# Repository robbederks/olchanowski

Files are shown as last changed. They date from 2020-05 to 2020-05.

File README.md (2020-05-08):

# Olchanowski
## Fixing the Zortrax M200 electronics
The Zortrax M200's mechanical design is great. It's electronics and software is not.
Let's fix that!

### Checklist
- [X] Processor
- [X] 4 stepper drivers
- [X] Ethernet
- [X] Fan control
- [X] 3 end stops
- [X] "senser"
- [X] RGB LED strip control
- [X] Heated bed
  - [X] Driver
  - [X] Thermocouple
- [X] Power input
- [X] Power regulation
- [X] USB
- [X] UI cable
  - [X] Connector
  - [X] OLED panel (UG-5664ALBEF01)
  - [X] Beeper
  - [X] Rotary encoder
  - [X] SD card
- [X] Extruder cable
  - [X] Connector (1-281742-2)
  - [X] Stepper
  - [X] Heater
  - [X] Thermocouple
  - [X] Fans
- [X] ICSP: UART
- [X] Filament sensor
- [X] LEDs
  - [X] GPIOs
  - [X] Voltage rail
  - [X] Heaters

## Version 1: Order list
| Description | MPN | QTY |
|---|---|-----|
| Extruder cable connector | 1-281742-2 | 1 |
| Heated bed connector | 1744428-4 | 1 |
| LCD connector | 302-S201 | 1 |
| Ethernet jack | ARJM11D7-009-AB-ER2-T | 1 |
| End switch + FAN + HB thermistor connector | B2B-XH-AM(LF)(SN) | 5 |
| Diode | BAT60AE6327HTSA1 | 2 |
| 470pF 0402 | C0402C471K5RACTU | 2 |
| 22nF 0402 | GRM155R71H223KA12J | 4 |
| 100 Ohm 0402 | CRG0402F100R | 2 |
| 10 kOhm 0402 | CRG0402F10K | 26  |
| 1 kOhm 0402 | CRG0402F1K | 3 |
| 1.5 kOhm 0402 | CRG0402F1K5 | 2 |
| 1 Mohm 0402 | CRG0402F1M | 1 |
| 22 Ohm 0402 | CRG0402F22R | 4 |
| 2.4 kOhm 0402 | CRG0402F2K4 | 1 |
| 33 Ohm 0402 | CRG0402F33R | 2 |
| 4.7 kOhm 0402 | CRG0402F4K7 | 2 |
| 50 Ohm 0402 | CRG0402F50R | 4 |
| 12MHz crystal | CX3225SB12000H0PSTC1  | 1 |
| 25MHz crystal | CX3225SB25000H0FLJCC  | 1 |
| 12.1 kOhm | ERJ-2RKF1212X | 1 |
| Push buttons | EVQ-Q2Y03W | 2 |
| 12pF 0402 | GRM1555C1E120GA01D | 10  |
| 4.7uF 0402 | GRM155R61A475MEAAD | 13  |
| 100nF 0402 | GRM155R61H104KE19D | 45  |
| 10uF 0805 | GRM21BR6YA106ME43L | 8 |
| Current sense resistor 0.1 Ohm 1206 | KRL1632E-M-R100-F-T5  | 8 |
| LM5551 | LM5111-1MX/NOPB | 1 |
| LPC1768 | "LPC1769FBD100,551" | 1 |
| LEDs 0603 | LTST-C190TBKT | 7 |
| Inductor | MLZ1608A1R0WT000 | 1 |
| PCA9306DCTR | PCA9306DCTR | 1 |
| 6 pin header | PPTC061LFBN-RC | 1 |
| Power MOSFET | SIJA58DP | 2 |
| N-Ch MOSFET | "SSM3K329R,LF" | 6 |
| Stepper driver | TMC2209-LA | 4 |
| 220uF elcaps | UCW1V221MNL1GS | 8 |
| Stepper + RGB + filament sensor connectors | B4B-XH-A(LF)(SN) | 5 |
| USB-C female connector | DX07S024XJ1R1100 | 1 |
| Power connector | 282814-4 | 1 |
| Power module | TPSM53602 | 1 |
| P-Ch MOSFET | DMP3099L-13 | 1 |
| Ethernet PHY | LAN8720A-CP-TR-ABC | 1 |
| Inverter | 74HC1G04 | 1 |
| 3.3V regulator | NCP5661MN33T2G | 1 |
| Senser connector | B3B-XH-A(LF)(SN) | 1 |

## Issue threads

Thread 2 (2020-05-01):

X1, X2, X3, X4 Part is missing mounting hole

vanillagorillaa, 2020-05-01:
B2B-XH-AMK(LF)(SN) is missing a mounting hole in the board

vanillagorillaa, 2020-05-09:
Fixed in 6538cdf7a0786e43772336199ad8634c6ffd7720

Closed 2020-05-09.

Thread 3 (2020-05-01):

Ethernet connector LED pins in wrong spot

vanillagorillaa, 2020-05-01:
ARJM11D7-009-AB-ER2-T Footprint is wrong. Current footprint uses 10/100/1000 connector footprint

vanillagorillaa, 2020-05-09:
Fixed in 37fe7109c28374d02037d3b275595f5fae3c16f2

Closed 2020-05-09.

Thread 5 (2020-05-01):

Ethernet connector footprint numbering wrong

robbederks, 2020-05-01:

vanillagorillaa, 2020-05-09:
Fixed in 37fe7109c28374d02037d3b275595f5fae3c16f2

Closed 2020-05-09.

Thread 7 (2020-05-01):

AGND not connected on P1

robbederks, 2020-05-01:
Also connect NC pins to GND like in datasheet (https://www.ti.com/lit/ds/symlink/tpsm53602.pdf?ts=1588302774740)

vanillagorillaa, 2020-05-08:
Fixed in 749eeb49f01eb6fa2927ce801f29494a110230ea

Closed 2020-05-08.

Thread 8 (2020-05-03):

Pin P0_27 and P0_28 are open-drain only: no LED driving!

robbederks, 2020-05-03:

vanillagorillaa, 2020-05-09:
Fixed in f67002b0d46e6c94cf34e9f857e3886063b88d9a

Closed 2020-05-09.

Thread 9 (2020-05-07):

Stepper connector winding pinout is wrong

robbederks, 2020-05-07:

vanillagorillaa, 2020-05-08:
Fixed in 95ee329ae1723655891ae612e65790c3f3b5e32d

Closed 2020-05-08.

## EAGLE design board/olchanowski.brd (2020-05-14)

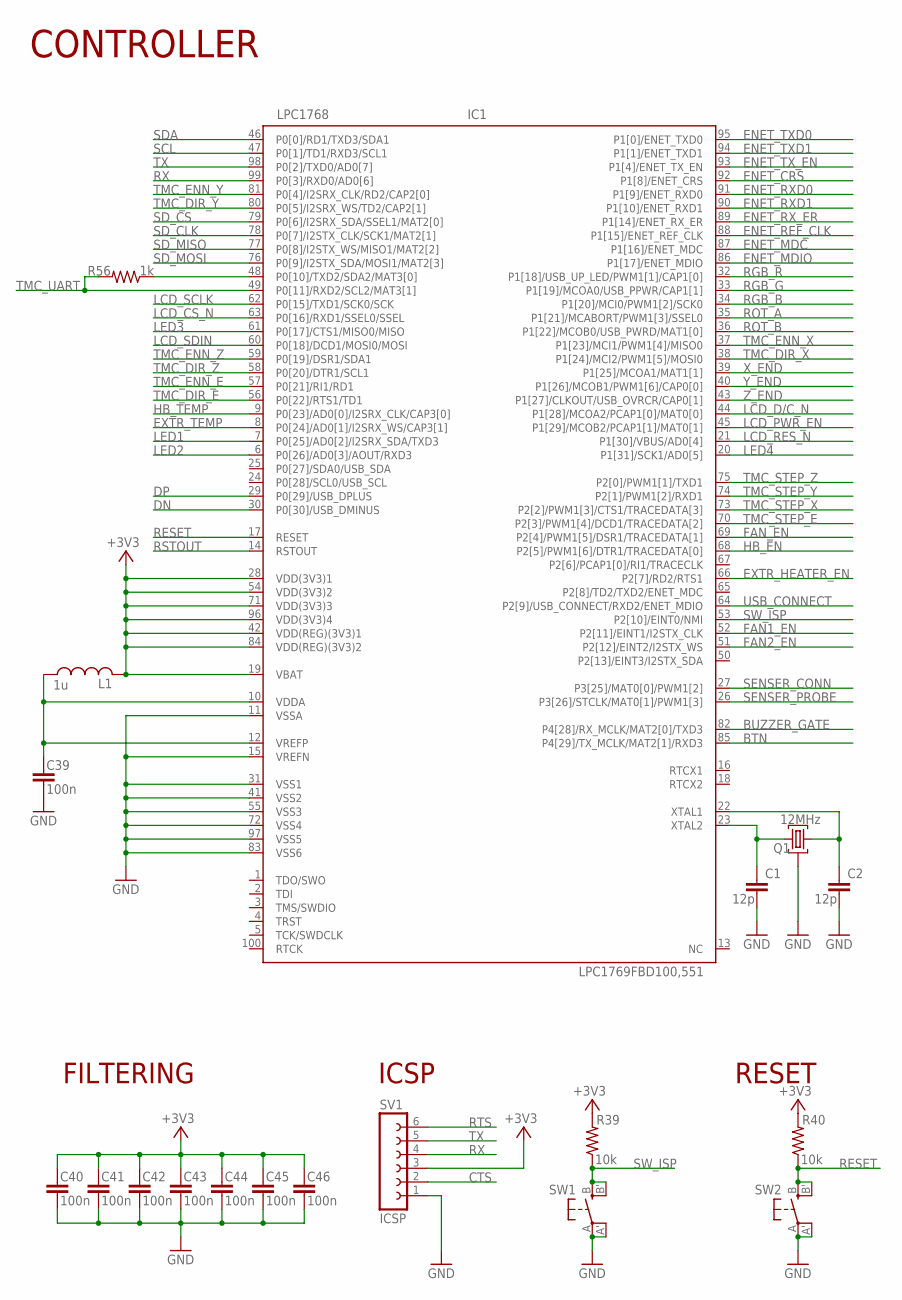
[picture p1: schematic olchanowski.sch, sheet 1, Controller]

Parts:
C1, C2: C; 0402; MPN GRM1555C1E120GA01D
C39, C40, C41, C42, C43, C44, C45, C46: C; 0402; MPN GRM155R61H104KE19D
IC1: LPC1768; LQFP100-14X14; MPN LPC1769FBD100,551
L1: L-USL0603; L0603; MPN MLZ1608A1R0WT000
Q1: 12MHz; CX3225SB; MPN CX3225SB12000H0PSTC1
R39, R40: R-US_R0402; R0402; MPN CRG0402F10K
R56: R-US_R0402; R0402; MPN CRG0402F1K
SV1: ICSP; FE06; MPN PPTC061LFBN-RC
SW1, SW2: SPST-2-4PIN; EVQ-Q2; MPN EVQ-Q2Y03W

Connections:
+3V3: C40.2, C41.2, C42.2, C43.2, C44.2, C45.2, C46.2, IC1.19 (VBAT), IC1.28 (VDD(3V3)1), IC1.42 (VDD(REG)(3V3)1), IC1.54 (VDD(3V3)2), IC1.71 (VDD(3V3)3), IC1.84 (VDD(REG)(3V3)2), IC1.96 (VDD(3V3)4), L1.2, R39.2, R40.2, SV1.3; also elsewhere on the board
BTN: IC1.85 (P4[29]/TX_MCLK/MAT2[1]/RXD3); also elsewhere on the board
BUZZER_GATE: IC1.82 (P4[28]/RX_MCLK/MAT2[0]/TXD3); also elsewhere on the board
CTS: SV1.2
DN: IC1.30 (P0[30]/USB_DMINUS); also elsewhere on the board
DP: IC1.29 (P0[29]/USB_DPLUS); also elsewhere on the board
ENET_CRS: IC1.92 (P1[8]/ENET_CRS); also elsewhere on the board
ENET_MDC: IC1.87 (P1[16]/ENET_MDC); also elsewhere on the board
ENET_MDIO: IC1.86 (P1[17]/ENET_MDIO); also elsewhere on the board
ENET_REF_CLK: IC1.88 (P1[15]/ENET_REF_CLK); also elsewhere on the board
ENET_RXD0: IC1.91 (P1[9]/ENET_RXD0); also elsewhere on the board
ENET_RXD1: IC1.90 (P1[10]/ENET_RXD1); also elsewhere on the board
ENET_RX_ER: IC1.89 (P1[14]/ENET_RX_ER); also elsewhere on the board
ENET_TXD0: IC1.95 (P1[0]/ENET_TXD0); also elsewhere on the board
ENET_TXD1: IC1.94 (P1[1]/ENET_TXD1); also elsewhere on the board
ENET_TX_EN: IC1.93 (P1[4]/ENET_TX_EN); also elsewhere on the board
EXTR_HEATER_EN: IC1.66 (P2[7]/RD2/RTS1); also elsewhere on the board
EXTR_TEMP: IC1.8 (P0[24]/AD0[1]/I2SRX_WS/CAP3[1]); also elsewhere on the board
FAN1_EN: IC1.52 (P2[11]/EINT1/I2STX_CLK); also elsewhere on the board
FAN2_EN: IC1.51 (P2[12]/EINT2/I2STX_WS); also elsewhere on the board
FAN_EN: IC1.69 (P2[4]/PWM1[5]/DSR1/TRACEDATA[1]); also elsewhere on the board
GND: C1.2, C2.2, C39.1, C40.1, C41.1, C42.1, C43.1, C44.1, C45.1, C46.1, IC1.11 (VSSA), IC1.15 (VREFN), IC1.31 (VSS1), IC1.41 (VSS2), IC1.55 (VSS3), IC1.72 (VSS4), IC1.83 (VSS6), IC1.97 (VSS5), Q1.GND1 (2), Q1.GND2 (2), SV1.1, SW1.A, SW1.A' (P1), SW2.A, SW2.A' (P1); also elsewhere on the board
HB_EN: IC1.68 (P2[5]/PWM1[6]/DTR1/TRACEDATA[0]); also elsewhere on the board
HB_TEMP: IC1.9 (P0[23]/AD0[0]/I2SRX_CLK/CAP3[0]); also elsewhere on the board
LCD_CS_N: IC1.63 (P0[16]/RXD1/SSEL0/SSEL); also elsewhere on the board
LCD_D/C_N: IC1.44 (P1[28]/MCOA2/PCAP1[0]/MAT0[0]); also elsewhere on the board
LCD_PWR_EN: IC1.45 (P1[29]/MCOB2/PCAP1[1]/MAT0[1]); also elsewhere on the board
LCD_RES_N: IC1.21 (P1[30]/VBUS/AD0[4]); also elsewhere on the board
LCD_SCLK: IC1.62 (P0[15]/TXD1/SCK0/SCK); also elsewhere on the board
LCD_SDIN: IC1.60 (P0[18]/DCD1/MOSI0/MOSI); also elsewhere on the board
LED1: IC1.7 (P0[25]/AD0[2]/I2SRX_SDA/TXD3); also elsewhere on the board
LED2: IC1.6 (P0[26]/AD0[3]/AOUT/RXD3); also elsewhere on the board
LED3: IC1.61 (P0[17]/CTS1/MISO0/MISO); also elsewhere on the board
LED4: IC1.20 (P1[31]/SCK1/AD0[5]); also elsewhere on the board
unnamed: C1.1, IC1.23 (XTAL2), Q1.XTAL1 (1)
unnamed: C2.1, IC1.22 (XTAL1), Q1.XTAL2 (3)
unnamed: C39.2, IC1.10 (VDDA), IC1.12 (VREFP), L1.1
unnamed: IC1.48 (P0[10]/TXD2/SDA2/MAT3[0]), R56.1
RESET: IC1.17 (RESET), R40.1, SW2.B (S), SW2.B' (S1)
RGB_B: IC1.34 (P1[20]/MCI0/PWM1[2]/SCK0); also elsewhere on the board
RGB_G: IC1.33 (P1[19]/MCOA0/USB_PPWR/CAP1[1]); also elsewhere on the board
RGB_R: IC1.32 (P1[18]/USB_UP_LED/PWM1[1]/CAP1[0]); also elsewhere on the board
ROT_A: IC1.35 (P1[21]/MCABORT/PWM1[3]/SSEL0); also elsewhere on the board
ROT_B: IC1.36 (P1[22]/MCOB0/USB_PWRD/MAT1[0]); also elsewhere on the board
RSTOUT: IC1.14 (RSTOUT); also elsewhere on the board
RTS: SV1.6
RX: IC1.99 (P0[3]/RXD0/AD0[6]), SV1.4
SCL: IC1.47 (P0[1]/TD1/RXD3/SCL1); also elsewhere on the board
SDA: IC1.46 (P0[0]/RD1/TXD3/SDA1); also elsewhere on the board
SD_CLK: IC1.78 (P0[7]/I2STX_CLK/SCK1/MAT2[1]); also elsewhere on the board
SD_CS: IC1.79 (P0[6]/I2SRX_SDA/SSEL1/MAT2[0]); also elsewhere on the board
SD_MISO: IC1.77 (P0[8]/I2STX_WS/MISO1/MAT2[2]); also elsewhere on the board
SD_MOSI: IC1.76 (P0[9]/I2STX_SDA/MOSI1/MAT2[3]); also elsewhere on the board
SENSER_CONN: IC1.27 (P3[25]/MAT0[0]/PWM1[2]); also elsewhere on the board
SENSER_PROBE: IC1.26 (P3[26]/STCLK/MAT0[1]/PWM1[3]); also elsewhere on the board
SW_ISP: IC1.53 (P2[10]/EINT0/NMI), R39.1, SW1.B (S), SW1.B' (S1)
TMC_DIR_E: IC1.56 (P0[22]/RTS1/TD1); also elsewhere on the board
TMC_DIR_X: IC1.38 (P1[24]/MCI2/PWM1[5]/MOSI0); also elsewhere on the board
TMC_DIR_Y: IC1.80 (P0[5]/I2SRX_WS/TD2/CAP2[1]); also elsewhere on the board
TMC_DIR_Z: IC1.58 (P0[20]/DTR1/SCL1); also elsewhere on the board
TMC_ENN_E: IC1.57 (P0[21]/RI1/RD1); also elsewhere on the board
TMC_ENN_X: IC1.37 (P1[23]/MCI1/PWM1[4]/MISO0); also elsewhere on the board
TMC_ENN_Y: IC1.81 (P0[4]/I2SRX_CLK/RD2/CAP2[0]); also elsewhere on the board
TMC_ENN_Z: IC1.59 (P0[19]/DSR1/SDA1); also elsewhere on the board
TMC_STEP_E: IC1.70 (P2[3]/PWM1[4]/DCD1/TRACEDATA[2]); also elsewhere on the board
TMC_STEP_X: IC1.73 (P2[2]/PWM1[3]/CTS1/TRACEDATA[3]); also elsewhere on the board
TMC_STEP_Y: IC1.74 (P2[1]/PWM1[2]/RXD1); also elsewhere on the board
TMC_STEP_Z: IC1.75 (P2[0]/PWM1[1]/TXD1); also elsewhere on the board
TMC_UART: IC1.49 (P0[11]/RXD2/SCL2/MAT3[1]), R56.2; also elsewhere on the board
TX: IC1.98 (P0[2]/TXD0/AD0[7]), SV1.5
USB_CONNECT: IC1.64 (P2[9]/USB_CONNECT/RXD2/ENET_MDIO); also elsewhere on the board
X_END: IC1.39 (P1[25]/MCOA1/MAT1[1]); also elsewhere on the board
Y_END: IC1.40 (P1[26]/MCOB1/PWM1[6]/CAP0[0]); also elsewhere on the board
Z_END: IC1.43 (P1[27]/CLKOUT/USB_OVRCR/CAP0[1]); also elsewhere on the board

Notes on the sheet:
CONTROLLER
ICSP
FILTERING
RESET

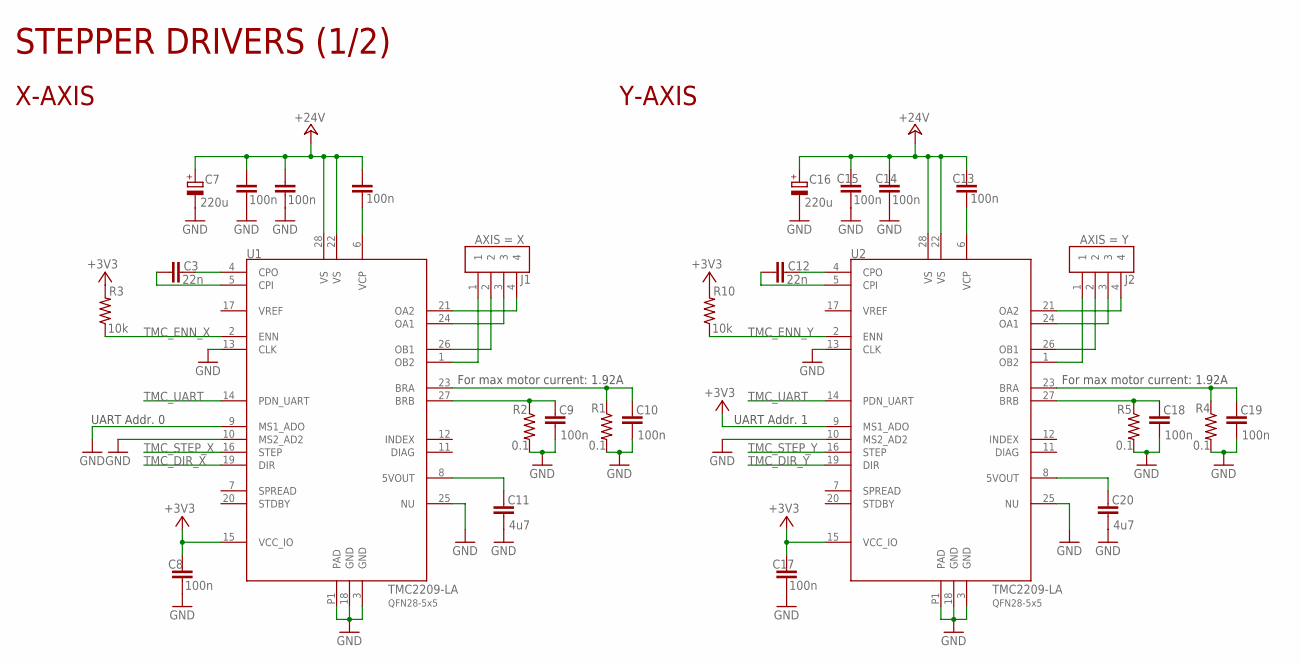
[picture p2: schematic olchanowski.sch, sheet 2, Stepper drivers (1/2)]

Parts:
C3, C12: C; 0402; MPN GRM155R71H223KA12J
C4, C5, C6, C8, C9, C10, C13, C14, C15, C17, C18, C19: C; 0402; MPN GRM155R61H104KE19D
C7, C16: CPOL-EU150CLZ-0810; 150CLZ-0810; MPN UCW1V221MNL1GS
C11, C20: C; 0402; MPN GRM155R61A475MEAAD
J1: X-AXIS; JST_B4B-XH-A(LF)(SN)
J2: Y-AXIS; JST_B4B-XH-A(LF)(SN)
R1, R2, R4, R5: R-US_R1206; R1206; MPN KRL1632E-M-R100-F-T5
R3, R10: R-US_R0402; R0402; MPN CRG0402F10K
U1, U2: TMC2209-LA; QFN28-5X5-XLEP

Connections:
+3V3: C8.2, C17.2, R3.2, R10.2, U1.15 (VCC_IO), U2.9 (MS1_ADO), U2.15 (VCC_IO); also elsewhere on the board
+24V: C4.2, C5.2, C6.2, C7.+, C13.2, C14.2, C15.2, C16.+, U1.22 (VS), U1.28 (VS), U2.22 (VS), U2.28 (VS); also elsewhere on the board
GND: C5.1, C6.1, C7.-, C8.1, C9.1, C10.1, C11.1, C14.1, C15.1, C16.-, C17.1, C18.1, C19.1, C20.1, R1.2, R2.2, R4.2, R5.2, U1.3 (GND), U1.9 (MS1_ADO), U1.10 (MS2_AD2), U1.13 (CLK), U1.18 (GND), U1.25 (NU), U1.P1 (PAD), U2.3 (GND), U2.10 (MS2_AD2), U2.13 (CLK), U2.18 (GND), U2.25 (NU), U2.P1 (PAD); also elsewhere on the board
unnamed: C3.2, U1.4 (CPO)
unnamed: C3.1, U1.5 (CPI)
unnamed: C4.1, U1.6 (VCP)
unnamed: C10.2, R1.1, U1.23 (BRA)
unnamed: C9.2, R2.1, U1.27 (BRB)
unnamed: J2.1, U2.1 (OB2)
unnamed: J2.2, U2.26 (OB1)
unnamed: J2.3, U2.24 (OA1)
unnamed: J2.4, U2.21 (OA2)
unnamed: C11.2, U1.8 (5VOUT)
unnamed: C12.2, U2.4 (CPO)
unnamed: C12.1, U2.5 (CPI)
unnamed: C13.1, U2.6 (VCP)
unnamed: C19.2, R4.1, U2.23 (BRA)
unnamed: C18.2, R5.1, U2.27 (BRB)
unnamed: C20.2, U2.8 (5VOUT)
unnamed: J1.4, U1.21 (OA2)
unnamed: J1.3, U1.24 (OA1)
unnamed: J1.2, U1.26 (OB1)
unnamed: J1.1, U1.1 (OB2)
TMC_DIR_X: U1.19 (DIR); also elsewhere on the board
TMC_DIR_Y: U2.19 (DIR); also elsewhere on the board
TMC_ENN_X: R3.1, U1.2 (ENN); also elsewhere on the board
TMC_ENN_Y: R10.1, U2.2 (ENN); also elsewhere on the board
TMC_STEP_X: U1.16 (STEP); also elsewhere on the board
TMC_STEP_Y: U2.16 (STEP); also elsewhere on the board
TMC_UART: U1.14 (PDN_UART), U2.14 (PDN_UART); also elsewhere on the board

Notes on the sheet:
STEPPER DRIVERS (1/2)
For max motor current: 1.92A
UART Addr. 0
X-AXIS
UART Addr. 1
Y-AXIS

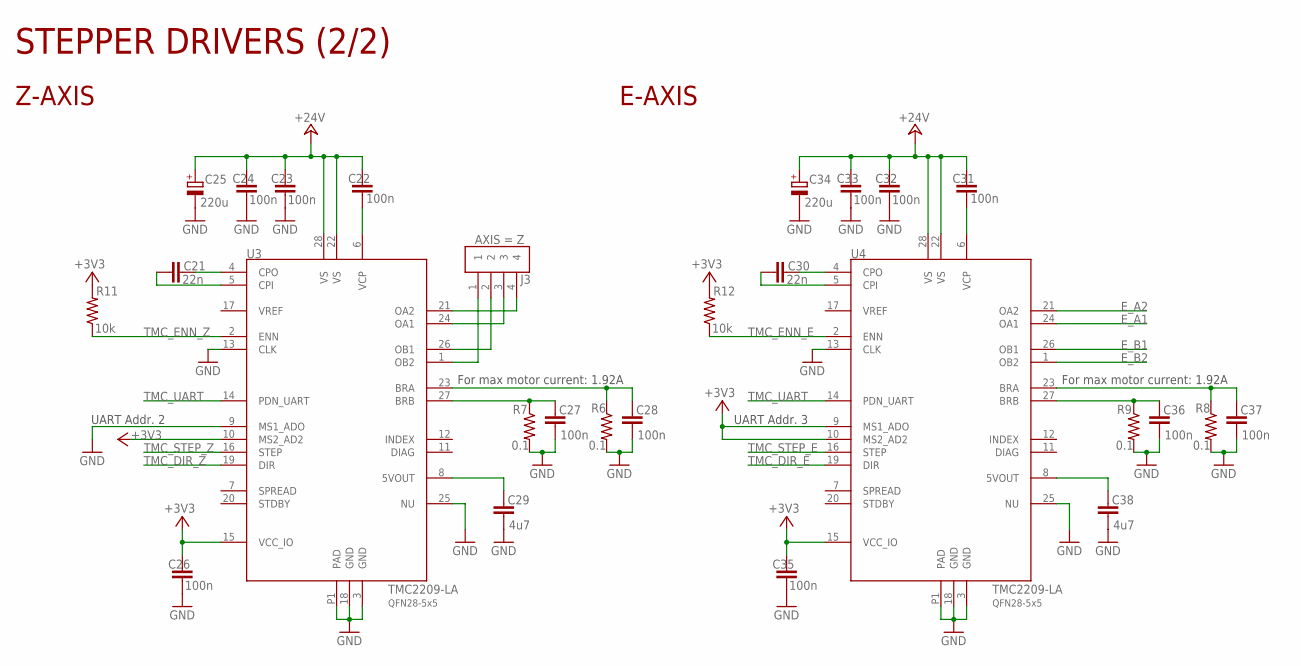
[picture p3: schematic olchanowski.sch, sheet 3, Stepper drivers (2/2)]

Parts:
C21, C30: C; 0402; MPN GRM155R71H223KA12J
C22, C23, C24, C26, C27, C28, C31, C32, C33, C35, C36, C37: C; 0402; MPN GRM155R61H104KE19D
C25, C34: CPOL-EU150CLZ-0810; 150CLZ-0810; MPN UCW1V221MNL1GS
C29, C38: C; 0402; MPN GRM155R61A475MEAAD
J3: Z_AXIS; JST_B4B-XH-A(LF)(SN)
R6, R7, R8, R9: R-US_R1206; R1206; MPN KRL1632E-M-R100-F-T5
R11, R12: R-US_R0402; R0402; MPN CRG0402F10K
U3, U4: TMC2209-LA; QFN28-5X5-XLEP

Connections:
+3V3: C26.2, C35.2, R11.2, R12.2, U3.10 (MS2_AD2), U3.15 (VCC_IO), U4.9 (MS1_ADO), U4.10 (MS2_AD2), U4.15 (VCC_IO); also elsewhere on the board
+24V: C22.2, C23.2, C24.2, C25.+, C31.2, C32.2, C33.2, C34.+, U3.22 (VS), U3.28 (VS), U4.22 (VS), U4.28 (VS); also elsewhere on the board
E_A1: U4.24 (OA1); also elsewhere on the board
E_A2: U4.21 (OA2); also elsewhere on the board
E_B1: U4.26 (OB1); also elsewhere on the board
E_B2: U4.1 (OB2); also elsewhere on the board
GND: C23.1, C24.1, C25.-, C26.1, C27.1, C28.1, C29.1, C32.1, C33.1, C34.-, C35.1, C36.1, C37.1, C38.1, R6.2, R7.2, R8.2, R9.2, U3.3 (GND), U3.9 (MS1_ADO), U3.13 (CLK), U3.18 (GND), U3.25 (NU), U3.P1 (PAD), U4.3 (GND), U4.13 (CLK), U4.18 (GND), U4.25 (NU), U4.P1 (PAD); also elsewhere on the board
unnamed: J3.1, U3.1 (OB2)
unnamed: J3.2, U3.26 (OB1)
unnamed: J3.3, U3.24 (OA1)
unnamed: J3.4, U3.21 (OA2)
unnamed: C21.2, U3.4 (CPO)
unnamed: C21.1, U3.5 (CPI)
unnamed: C22.1, U3.6 (VCP)
unnamed: C28.2, R6.1, U3.23 (BRA)
unnamed: C27.2, R7.1, U3.27 (BRB)
unnamed: C29.2, U3.8 (5VOUT)
unnamed: C30.2, U4.4 (CPO)
unnamed: C30.1, U4.5 (CPI)
unnamed: C31.1, U4.6 (VCP)
unnamed: C37.2, R8.1, U4.23 (BRA)
unnamed: C36.2, R9.1, U4.27 (BRB)
unnamed: C38.2, U4.8 (5VOUT)
TMC_DIR_E: U4.19 (DIR); also elsewhere on the board
TMC_DIR_Z: U3.19 (DIR); also elsewhere on the board
TMC_ENN_E: R12.1, U4.2 (ENN); also elsewhere on the board
TMC_ENN_Z: R11.1, U3.2 (ENN); also elsewhere on the board
TMC_STEP_E: U4.16 (STEP); also elsewhere on the board
TMC_STEP_Z: U3.16 (STEP); also elsewhere on the board
TMC_UART: U3.14 (PDN_UART), U4.14 (PDN_UART); also elsewhere on the board

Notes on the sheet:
STEPPER DRIVERS (2/2)
For max motor current: 1.92A
UART Addr. 2
Z-AXIS
UART Addr. 3
E-AXIS

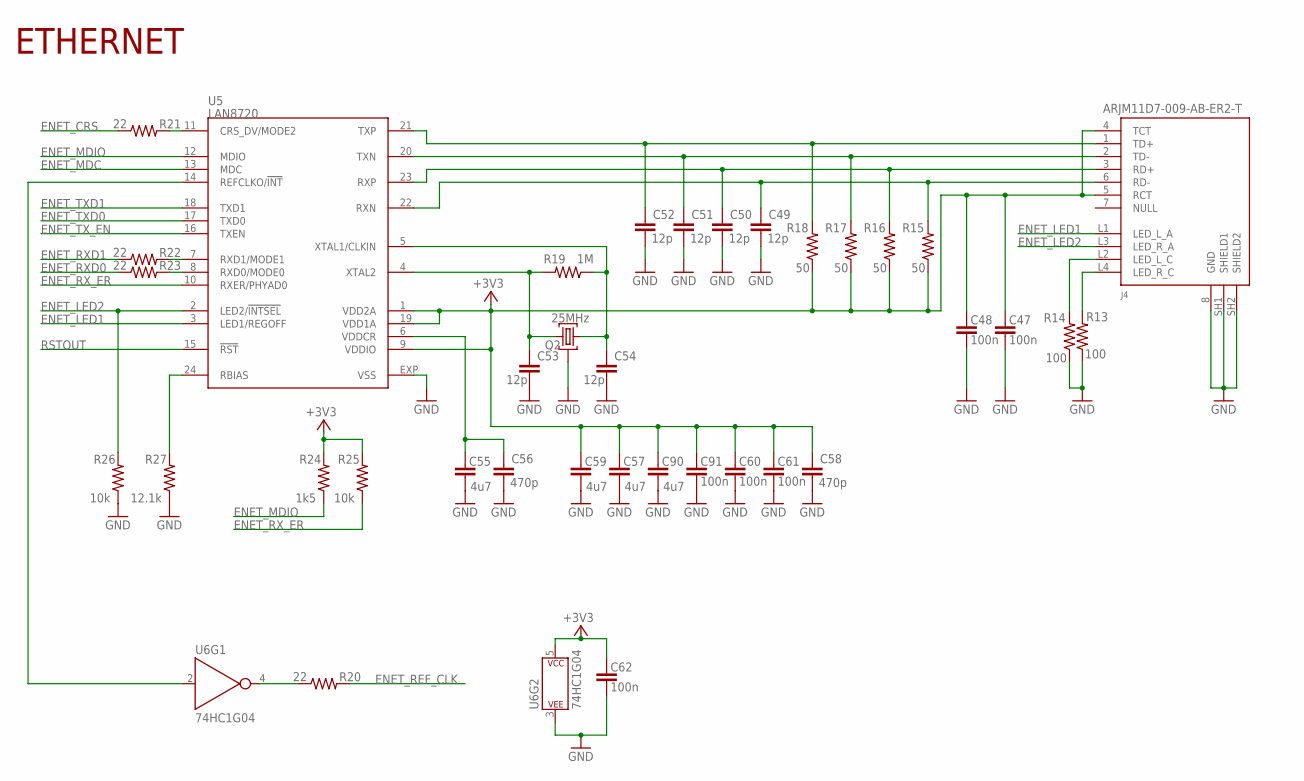
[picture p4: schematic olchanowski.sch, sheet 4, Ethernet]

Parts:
C47, C48, C60, C61, C62, C91: C; 0402; MPN GRM155R61H104KE19D
C49, C50, C51, C52, C53, C54: C; 0402; MPN GRM1555C1E120GA01D
C55, C57, C59, C90: C; 0402; MPN GRM155R61A475MEAAD
C56, C58: C; 0402; MPN C0402C471K5RACTU
J4: ARJM11D7-009-AB-ER2-T; ARJM11D7-009-AB; MPN ARJM11D7-009-AB-ER2-T
Q2: 25MHz; CX3225SB; MPN CX3225SB25000H0FLJCC
R13, R14: R-US_R0402; R0402; MPN CRG0402F100R
R15, R16, R17, R18: R-US_R0402; R0402; MPN CRG0402F50R
R19: R-US_R0402; R0402; MPN CRG0402F1M
R20, R21, R22, R23: R-US_R0402; R0402; MPN CRG0402F22R
R24: R-US_R0402; R0402; MPN CRG0402F1K5
R25, R26: R-US_R0402; R0402; MPN CRG0402F10K
R27: R-US_R0402; R0402; MPN ERJ-2RKF1212X
U5: LAN8720; QFN24; MPN LAN8720A-CP-TR-ABC
U6: 74HC1G04; SOT353

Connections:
+3V3: C47.2, C48.2, C57.2, C58.1, C59.2, C60.2, C61.2, C62.2, C90.2, C91.2, J4.4 (TCT), J4.5 (RCT), R15.1, R16.1, R17.1, R18.1, R24.2, R25.2, U5.1 (VDD2A), U5.9 (VDDIO), U5.19 (VDD1A), U6.5 (P$V+); also elsewhere on the board
ENET_CRS: R21.1; also elsewhere on the board
ENET_LED1: J4.L1 (LED_L_A), U5.3 (LED1/REGOFF)
ENET_LED2: J4.L3 (LED_R_A), R26.2, U5.2 (LED2/!INTSEL)
ENET_MDC: U5.13 (MDC); also elsewhere on the board
ENET_MDIO: R24.1, U5.12 (MDIO); also elsewhere on the board
ENET_REF_CLK: R20.2; also elsewhere on the board
ENET_RXD0: R23.1; also elsewhere on the board
ENET_RXD1: R22.1; also elsewhere on the board
ENET_RX_ER: R25.1, U5.10 (RXER/PHYAD0); also elsewhere on the board
ENET_TXD0: U5.17 (TXD0); also elsewhere on the board
ENET_TXD1: U5.18 (TXD1); also elsewhere on the board
ENET_TX_EN: U5.16 (TXEN); also elsewhere on the board
GND: C47.1, C48.1, C49.2, C50.2, C51.2, C52.2, C53.2, C54.2, C55.1, C56.2, C57.1, C58.2, C59.1, C60.1, C61.1, C62.1, C90.1, C91.1, J4.8 (GND), J4.SH1 (SHIELD1), J4.SH2 (SHIELD2), Q2.GND1 (2), Q2.GND2 (2), R13.1, R14.1, R26.1, R27.1, U5.EXP (VSS), U6.3 (P$V-); also elsewhere on the board
unnamed: C52.1, J4.1 (TD+), R18.2, U5.21 (TXP)
unnamed: C51.1, J4.2 (TD-), R17.2, U5.20 (TXN)
unnamed: C50.1, J4.3 (RD+), R16.2, U5.23 (RXP)
unnamed: C49.1, J4.6 (RD-), R15.2, U5.22 (RXN)
unnamed: J4.L4 (LED_R_C), R13.2
unnamed: J4.L2 (LED_L_C), R14.2
unnamed: U5.14 (REFCLKO/!INT), U6.2 (A)
unnamed: C54.1, Q2.XTAL2 (3), R19.1, U5.5 (XTAL1/CLKIN)
unnamed: C55.2, C56.1, U5.6 (VDDCR)
unnamed: R20.1, U6.4 (Y)
unnamed: R21.2, U5.11 (CRS_DV/MODE2)
unnamed: R22.2, U5.7 (RXD1/MODE1)
unnamed: R23.2, U5.8 (RXD0/MODE0)
unnamed: R27.2, U5.24 (RBIAS)
unnamed: C53.1, Q2.XTAL1 (1), R19.2, U5.4 (XTAL2)
RSTOUT: U5.15 (!RST); also elsewhere on the board

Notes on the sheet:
ETHERNET

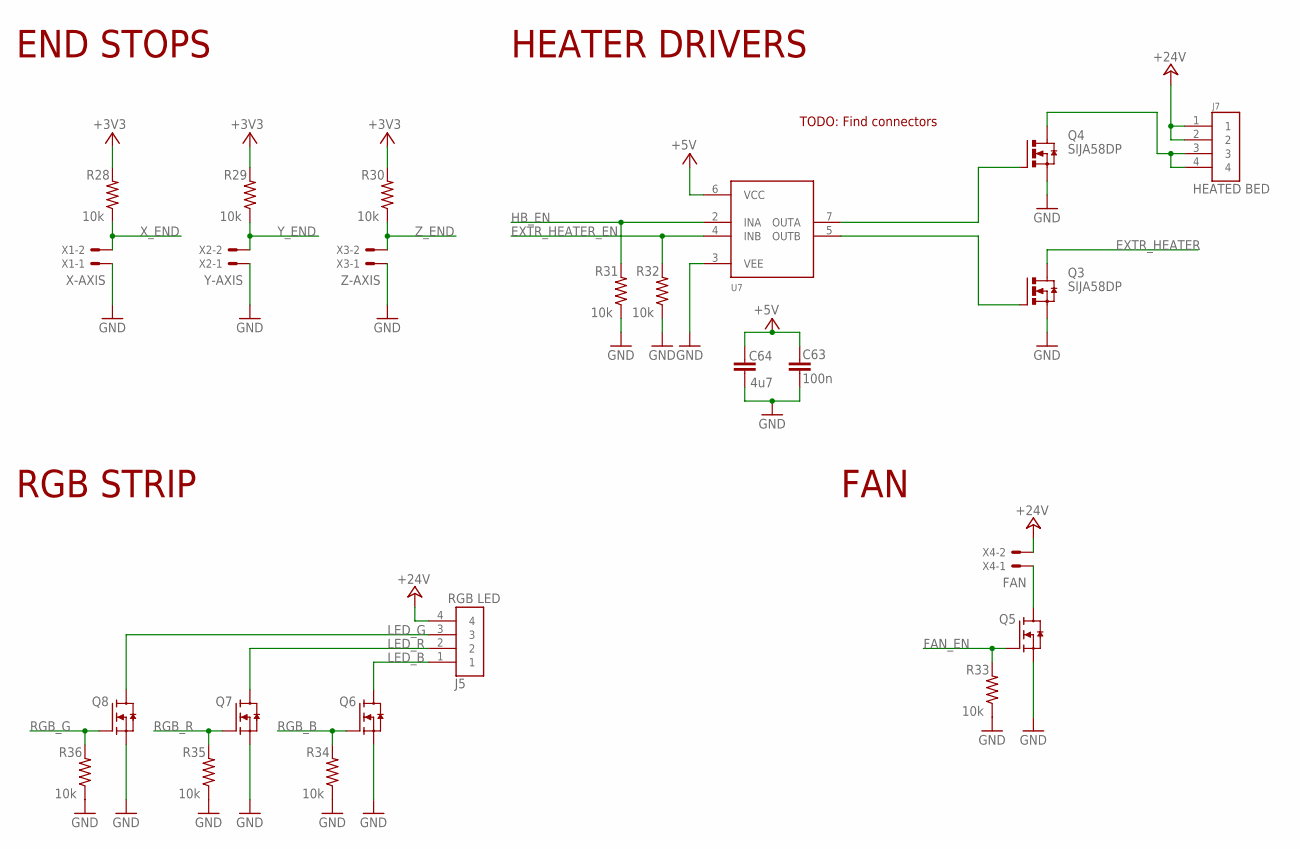
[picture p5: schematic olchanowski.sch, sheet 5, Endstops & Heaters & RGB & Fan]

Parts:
C63: C; 0402; MPN GRM155R61H104KE19D
C64: C; 0402; MPN GRM155R61A475MEAAD
J5: RGB LED; JST_B4B-XH-A(LF)(SN)
J7: 1744428-4; MPN 1744428-4
Q3, Q4: SIJA58DP; POWERPAK_SO-8L; MPN SIJA58DP
Q5, Q6, Q7, Q8: SSM3K329R,LF; SOT23; MPN SSM3K329R,LF
R28, R29, R30, R31, R32, R33, R34, R35, R36: R-US_R0402; R0402; MPN CRG0402F10K
U7: LM5111; SOIC8; MPN LM5111-1MX/NOPB
X1: X-AXIS; JST-XH-02-PACKAGE-LONG-PAD; MPN B2B-XH
X2: Y-AXIS; JST-XH-02-PACKAGE-LONG-PAD; MPN B2B-XH
X3: Z-AXIS; JST-XH-02-PACKAGE-LONG-PAD; MPN B2B-XH
X4: FAN; JST-XH-02-PACKAGE-LONG-PAD; MPN B2B-XH

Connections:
+3V3: R28.2, R29.2, R30.2; also elsewhere on the board
+5V: C63.2, C64.2, U7.6 (VCC); also elsewhere on the board
+24V: J5.4, J7.1, J7.2, X4.2; also elsewhere on the board
EXTR_HEATER: Q3.D1 (D), Q3.D2 (D), Q3.D3 (D); also elsewhere on the board
EXTR_HEATER_EN: R32.2, U7.4 (INB); also elsewhere on the board
FAN_EN: Q5.1 (G), R33.2; also elsewhere on the board
GND: C63.1, C64.1, Q3.S1 (S), Q3.S2 (S), Q3.S3 (S), Q4.S1 (S), Q4.S2 (S), Q4.S3 (S), Q5.2 (S), Q6.2 (S), Q7.2 (S), Q8.2 (S), R31.1, R32.1, R33.1, R34.1, R35.1, R36.1, U7.3 (VEE), X1.1, X2.1, X3.1; also elsewhere on the board
HB_EN: R31.2, U7.2 (INA); also elsewhere on the board
LED_B: J5.1, Q6.3 (D)
LED_G: J5.3, Q8.3 (D)
LED_R: J5.2, Q7.3 (D)
unnamed: Q4.G, U7.7 (OUTA)
unnamed: Q3.G, U7.5 (OUTB)
unnamed: Q5.3 (D), X4.1
unnamed: J7.3, J7.4, Q4.D1 (D), Q4.D2 (D), Q4.D3 (D)
RGB_B: Q6.1 (G), R34.2; also elsewhere on the board
RGB_G: Q8.1 (G), R36.2; also elsewhere on the board
RGB_R: Q7.1 (G), R35.2; also elsewhere on the board
X_END: R28.1, X1.2; also elsewhere on the board
Y_END: R29.1, X2.2; also elsewhere on the board
Z_END: R30.1, X3.2; also elsewhere on the board

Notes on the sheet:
END STOPS
HEATER DRIVERS
TODO: Find connectors
FAN
RGB STRIP

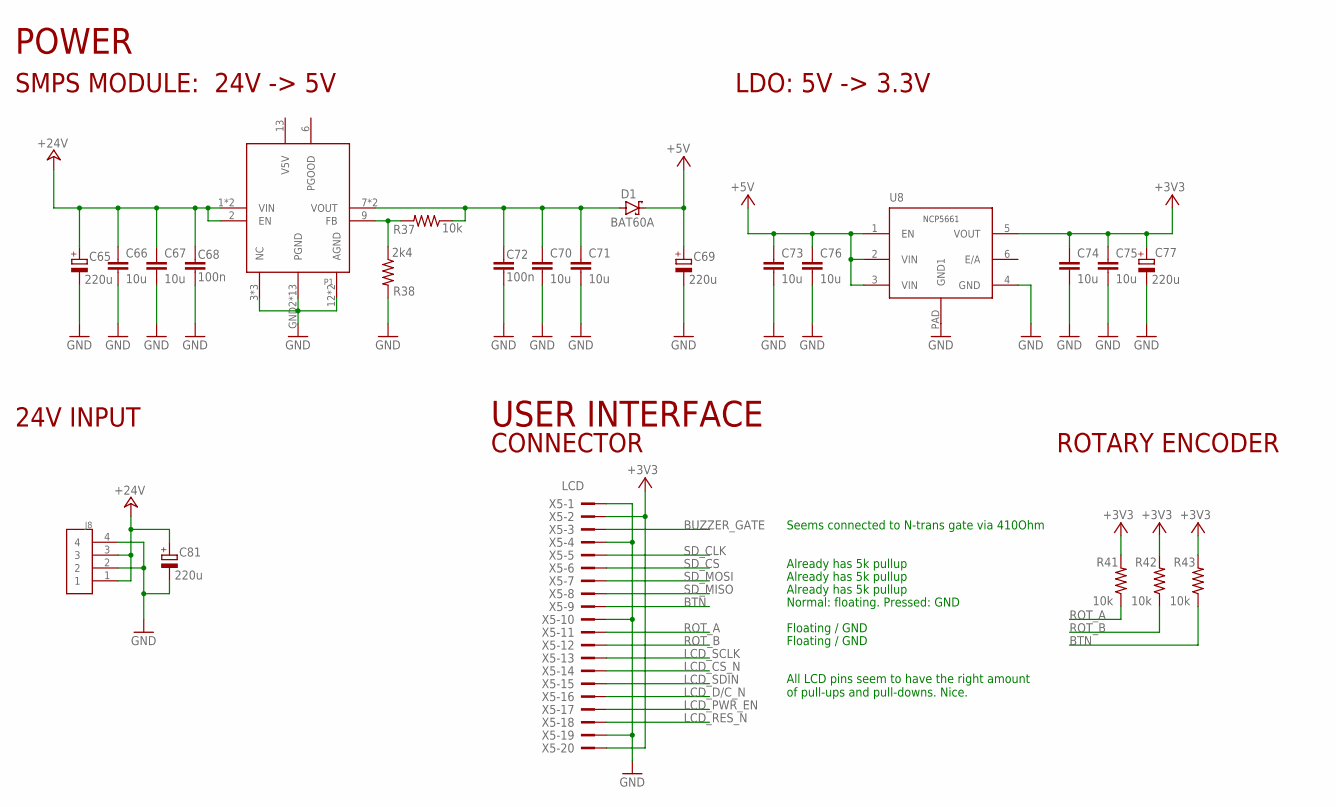
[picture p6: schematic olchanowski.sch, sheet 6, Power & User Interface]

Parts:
C65, C69, C77, C81: CPOL-EU150CLZ-0810; 150CLZ-0810; MPN UCW1V221MNL1GS
C66, C67, C70, C71, C73, C74, C75, C76: 10u; C0805; MPN GRM21BR6YA106ME43L
C68, C72: C; 0402; MPN GRM155R61H104KE19D
D1: BAT60A; SOD323_ST; MPN BAT60AE6327HTSA1
J8: 282814-4
P1: TPSM53602; B3QFN
R37, R41, R42, R43: R-US_R0402; R0402; MPN CRG0402F10K
R38: R-US_R0402; R0402; MPN CRG0402F2K4
U8: NCP5661-0; DFN6
X5: LCD; PAK100/2500-20; MPN 302-S201

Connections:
+3V3: C74.1, C75.1, C77.+, R41.2, R42.2, R43.2, U8.5 (VOUT), X5.2, X5.20; also elsewhere on the board
+5V: C69.+, C73.1, C76.1, D1.C, U8.1 (EN), U8.2 (VIN), U8.3 (VIN); also elsewhere on the board
+24V: C65.+, C66.1, C67.1, C68.2, C81.+, J8.1, J8.3, P1.1 (VIN), P1.2 (EN), P1.14 (VIN); also elsewhere on the board
BTN: R43.1, X5.9; also elsewhere on the board
BUZZER_GATE: X5.3; also elsewhere on the board
GND: C65.-, C66.2, C67.2, C68.1, C69.-, C70.2, C71.2, C72.1, C73.2, C74.2, C75.2, C76.2, C77.-, C81.-, J8.2, J8.4, P1.3 (NC), P1.10 (NC), P1.11 (NC), P1.12 (AGND), P1.GND1 (AGND), P1.GND2 (PGND), P1.GND3 (PGND), P1.GND4 (PGND), P1.GND5 (PGND), P1.GND6 (PGND), P1.GND7 (PGND), P1.GND8 (PGND), P1.GND9 (PGND), P1.GND10 (PGND), P1.GND11 (PGND), P1.GND12 (PGND), P1.GND13 (PGND), P1.GND14 (PGND), R38.2, U8.4 (GND), U8.PAD (GND1), X5.1, X5.4, X5.10, X5.19; also elsewhere on the board
LCD_CS_N: X5.14; also elsewhere on the board
LCD_D/C_N: X5.16; also elsewhere on the board
LCD_PWR_EN: X5.17; also elsewhere on the board
LCD_RES_N: X5.18; also elsewhere on the board
LCD_SCLK: X5.13; also elsewhere on the board
LCD_SDIN: X5.15; also elsewhere on the board
unnamed: P1.9 (FB), R37.2, R38.1
unnamed: C70.1, C71.1, C72.2, D1.A, P1.7 (VOUT), P1.8 (VOUT), R37.1
ROT_A: R41.1, X5.11; also elsewhere on the board
ROT_B: R42.1, X5.12; also elsewhere on the board
SD_CLK: X5.5; also elsewhere on the board
SD_CS: X5.6; also elsewhere on the board
SD_MISO: X5.8; also elsewhere on the board
SD_MOSI: X5.7; also elsewhere on the board

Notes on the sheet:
POWER
SMPS MODULE: 24V -> 5V
LDO: 5V -> 3.3V
USER INTERFACE
Normal: floating. Pressed: GND
Seems connected to N-trans gate via 410Ohm
Floating / GND
Already has 5k pullup
All LCD pins seem to have the right amount of pull-ups and pull-downs. Nice.
CONNECTOR
ROTARY ENCODER
24V INPUT

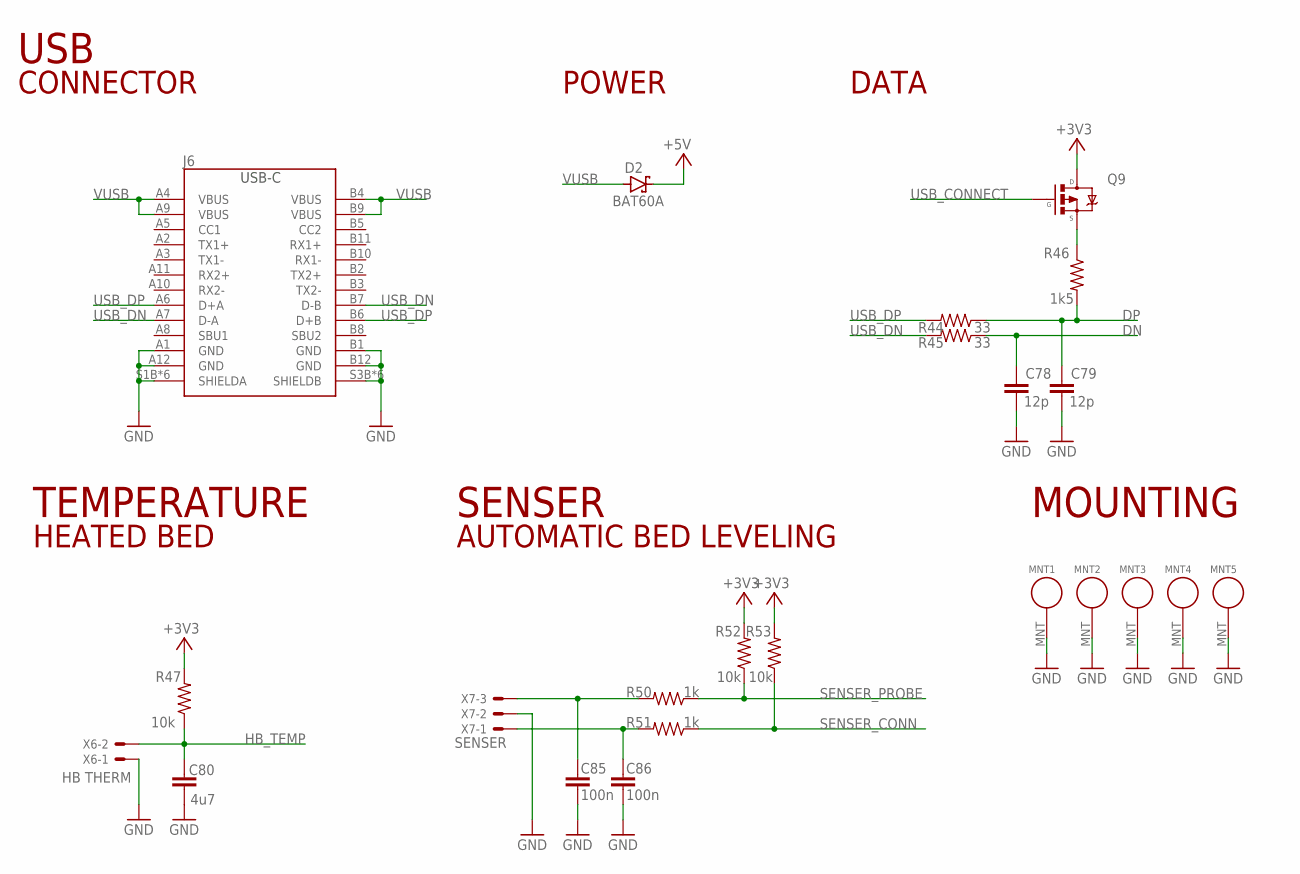
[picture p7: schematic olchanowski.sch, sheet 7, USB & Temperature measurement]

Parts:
C78, C79: C; 0402; MPN GRM1555C1E120GA01D
C80: C; 0402; MPN GRM155R61A475MEAAD
C85, C86: C; 0402; MPN GRM155R61H104KE19D
D2: BAT60A; SOD323_ST; MPN BAT60AE6327HTSA1
J6: USB-C-FEMALE; DX07S024XJ1R1100
MNT1, MNT2, MNT3, MNT4, MNT5: MOUNT; MOUNT-M3
Q9: PFETSM; SOT23-3; MPN DMP3099L-13
R44, R45: R-US_R0402; R0402; MPN CRG0402F33R
R46: R-US_R0402; R0402; MPN CRG0402F1K5
R47, R52, R53: R-US_R0402; R0402; MPN CRG0402F10K
R50, R51: R-US_R0402; R0402; MPN CRG0402F1K
X6: HB THERM; JST-XH-02-PACKAGE-LONG-PAD; MPN B2B-XH
X7: SENSER; JST-XH-03-PACKAGE-LONG-PAD

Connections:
+3V3: Q9.3 (D), R47.2, R52.2, R53.2; also elsewhere on the board
+5V: D2.C; also elsewhere on the board
DN: C78.1, R45.1; also elsewhere on the board
DP: C79.1, R44.1, R46.2; also elsewhere on the board
GND: C78.2, C79.2, C80.1, C85.1, C86.1, J6.A1 (GND), J6.A12 (GND), J6.B1 (GND), J6.B12 (GND), J6.S1B (SHIELDA), J6.S1T (SHIELDA), J6.S1TH (SHIELDA), J6.S2B (SHIELDA), J6.S2T (SHIELDA), J6.S2TH (SHIELDA), J6.S3B (SHIELDB), J6.S3T (SHIELDB), J6.S3TH (SHIELDB), J6.S4B (SHIELDB), J6.S4T (SHIELDB), J6.S4TH (SHIELDB), MNT1.MNT, MNT2.MNT, MNT3.MNT, MNT4.MNT, MNT5.MNT, X6.1, X7.2; also elsewhere on the board
HB_TEMP: C80.2, R47.1, X6.2; also elsewhere on the board
unnamed: Q9.2 (S), R46.1
unnamed: C85.2, R50.2, X7.3
unnamed: C86.2, R51.2, X7.1
SENSER_CONN: R51.1, R53.1; also elsewhere on the board
SENSER_PROBE: R50.1, R52.1; also elsewhere on the board
USB_CONNECT: Q9.1 (G); also elsewhere on the board
USB_DN: J6.A7 (D-A), J6.B7 (D-B), R45.2
USB_DP: J6.A6 (D+A), J6.B6 (D+B), R44.2
VUSB: D2.A, J6.A4 (VBUS), J6.A9 (VBUS), J6.B4 (VBUS), J6.B9 (VBUS)

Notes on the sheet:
USB
CONNECTOR
POWER
DATA
TEMPERATURE
HEATED BED
SENSER
AUTOMATIC BED LEVELING
MOUNTING

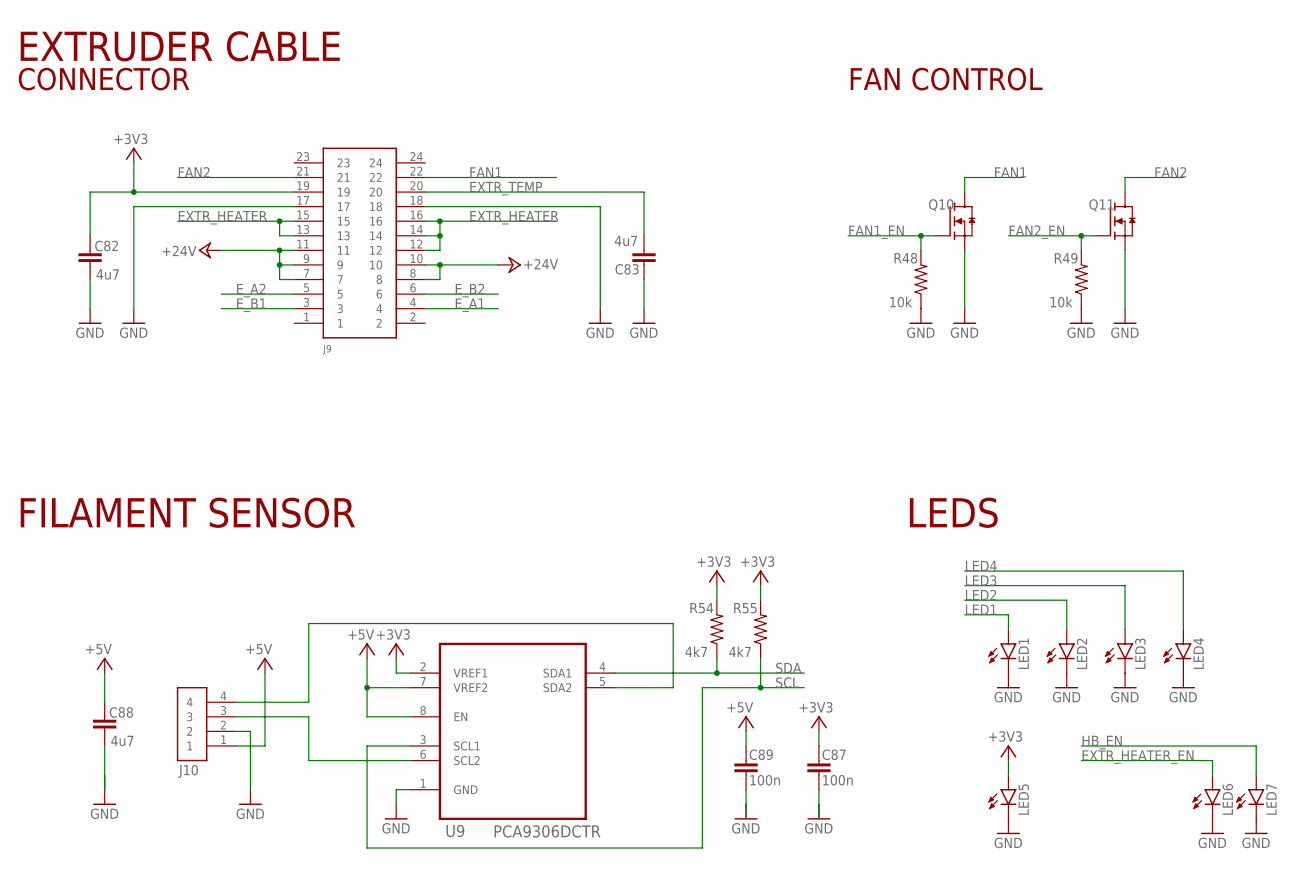
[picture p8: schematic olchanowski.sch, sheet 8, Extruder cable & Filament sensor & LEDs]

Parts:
C82, C83, C88: C; 0402; MPN GRM155R61A475MEAAD
C87, C89: C; 0402; MPN GRM155R61H104KE19D
J9: 1-281742-2; MPN 1-281742-2
J10: B4B-XH-A(LF)(SN); JST_B4B-XH-A(LF)(SN)
LED1, LED2, LED3, LED4, LED5, LED6, LED7: LEDCHIP-LED0603; CHIP-LED0603; MPN LTST-C190TBKT
Q10, Q11: SSM3K329R,LF; SOT23; MPN SSM3K329R,LF
R48, R49: R-US_R0402; R0402; MPN CRG0402F10K
R54, R55: R-US_R0402; R0402; MPN CRG0402F4K7
U9: PCA9306DCTR; SOP65P400X130-8N

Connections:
+3V3: C82.2, C87.2, J9.19, LED5.A, R54.2, R55.2, U9.2 (VREF1); also elsewhere on the board
+5V: C88.2, C89.2, J10.1, U9.7 (VREF2), U9.8 (EN); also elsewhere on the board
+24V: J9.7, J9.8, J9.9, J9.10, J9.11; also elsewhere on the board
EXTR_HEATER: J9.12, J9.13, J9.14, J9.15, J9.16; also elsewhere on the board
EXTR_HEATER_EN: LED6.A; also elsewhere on the board
EXTR_TEMP: C83.1, J9.20; also elsewhere on the board
E_A1: J9.4; also elsewhere on the board
E_A2: J9.5; also elsewhere on the board
E_B1: J9.3; also elsewhere on the board
E_B2: J9.6; also elsewhere on the board
FAN1: J9.22, Q10.3 (D)
FAN1_EN: Q10.1 (G), R48.2; also elsewhere on the board
FAN2: J9.21, Q11.3 (D)
FAN2_EN: Q11.1 (G), R49.2; also elsewhere on the board
GND: C82.1, C83.2, C87.1, C88.1, C89.1, J9.17, J9.18, J10.2, LED1.C, LED2.C, LED3.C, LED4.C, LED5.C, LED6.C, LED7.C, Q10.2 (S), Q11.2 (S), R48.1, R49.1, U9.1 (GND); also elsewhere on the board
HB_EN: LED7.A; also elsewhere on the board
LED1: LED1.A; also elsewhere on the board
LED2: LED2.A; also elsewhere on the board
LED3: LED3.A; also elsewhere on the board
LED4: LED4.A; also elsewhere on the board
unnamed: J10.3, U9.6 (SCL2)
unnamed: J10.4, U9.5 (SDA2)
SCL: R55.1, U9.3 (SCL1); also elsewhere on the board
SDA: R54.1, U9.4 (SDA1); also elsewhere on the board

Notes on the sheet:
EXTRUDER CABLE
FAN CONTROL
CONNECTOR
FILAMENT SENSOR
LEDS

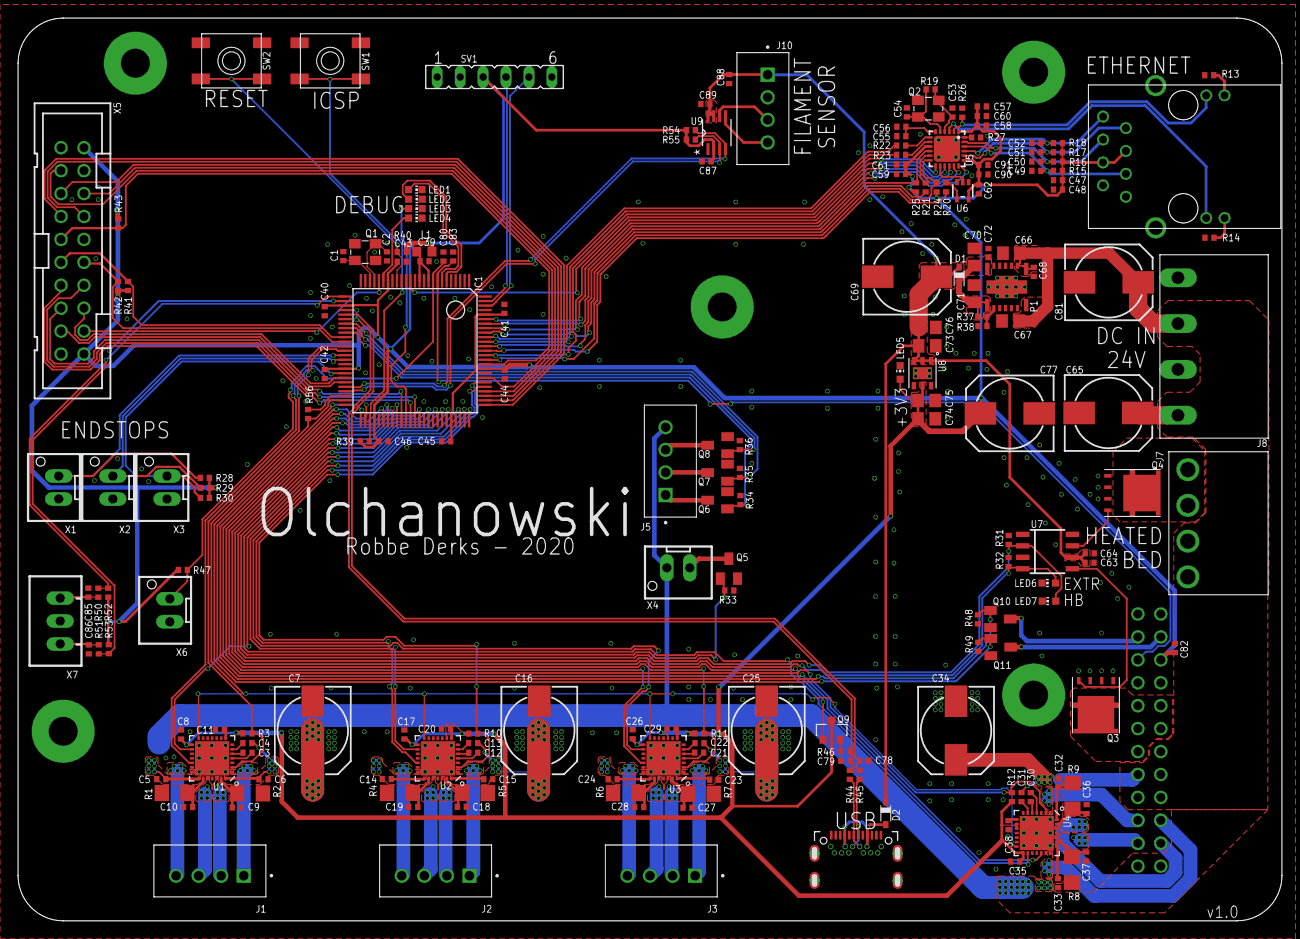
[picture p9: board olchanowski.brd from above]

Board: 2 copper layers, 140.0 x 100.0 mm, 203 parts (1 on the bottom side), 151 nets.

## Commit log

2020-04-04 Microcontroller and stepper drivers
    [olchanowski.sch]
2020-04-05 Added ethernet
    [olchanowski.sch]
2020-04-07 Endstops and heater drivers
    [olchanowski.sch]
2020-04-08 Added filament sensor to TODO
2020-04-08 More schematic stuff
    [olchanowski.sch]
2020-04-09 More schematic work
    [olchanowski.sch]
2020-04-10 More stuff
    [olchanowski.sch]
2020-04-11 Schematic finished!
    [olchanowski.sch]
2020-04-12 Started on board
    [olchanowski.brd, olchanowski.sch]
2020-04-14 Minor schematic improvements and initial routing work
    [olchanowski.brd, olchanowski.sch]
2020-04-15 Component placement
    [olchanowski.brd, olchanowski.sch]
2020-04-15 Example routing for a stepper driver
    [olchanowski.brd, olchanowski.sch]
2020-04-16 More routing
    [olchanowski.brd, olchanowski.sch]
2020-04-17 First rev done and ordered!
    [olchanowski.brd, olchanowski.sch]
2020-04-22 Added order list
    [olchanowski.brd, olchanowski.csv, olchanowski.sch]
2020-05-08 Fix label size
    [olchanowski.brd]
2020-05-08 Update Cap P/N
    [olchanowski.brd, olchanowski.sch]
2020-05-08 Fix P1 NC/AGND pins
    [olchanowski.brd, olchanowski.sch]
2020-05-08 Fix Stepper connector pinout
    [olchanowski.brd, olchanowski.sch]
2020-05-08 Add MPN for Q9
    [olchanowski.brd, olchanowski.sch]
2020-05-09 Fix Ethernet pinout and LED position
    [olchanowski.brd, olchanowski.sch]
2020-05-09 Move LED3 and LED4 on micro
    [olchanowski.brd, olchanowski.sch]
2020-05-09 Drill hole for JST plus some clean ups
    [olchanowski.brd, olchanowski.sch]
2020-05-14 Swap PROBE and CONN
    [olchanowski.brd, olchanowski.sch]

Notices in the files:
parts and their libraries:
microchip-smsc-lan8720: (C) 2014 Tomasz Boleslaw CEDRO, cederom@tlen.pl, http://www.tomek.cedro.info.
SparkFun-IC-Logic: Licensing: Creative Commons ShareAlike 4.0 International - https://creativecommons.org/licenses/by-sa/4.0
